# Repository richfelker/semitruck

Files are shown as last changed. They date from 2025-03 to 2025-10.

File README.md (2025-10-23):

# The Semitruck Extruder

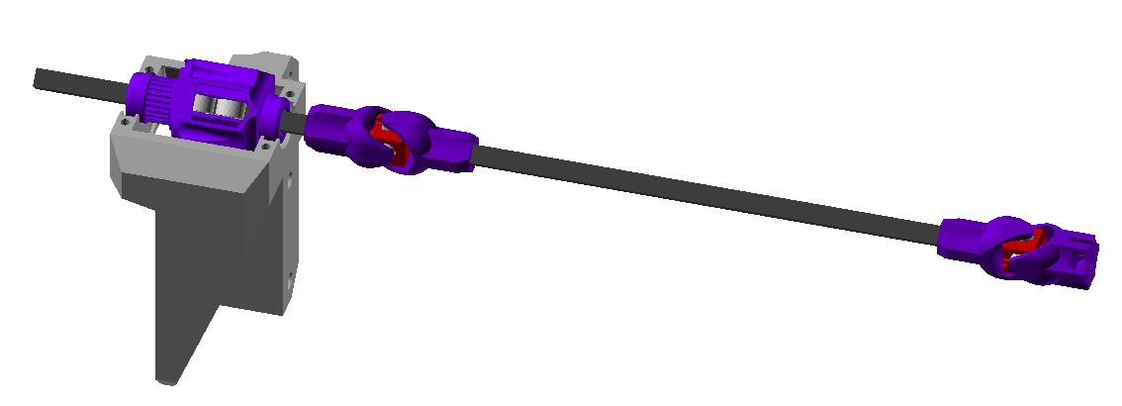
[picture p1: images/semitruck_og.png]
CAD diagram of Semitruck shaft


The Semitruck is a *rigid* remote direct drive (RDD) extruder based on
printed Cardan joints, square carbon fiber shaft, and a coupling that
transfers rotational force through ball bearings that can freely roll
along the four faces of the square shaft. It comes in two variants:

- OG Semitruck, where the vertical segment of the drive shaft engages
  with a fixed-position "slider gear" at the top of the printer and is
  free to move up and down, and

- Semitruck Prime, with a telescoping double Cardan shaft coupled
  directly to the motor at the top of the printer.

In either variant, the shaft drives an ultra-compact worm-based
extruder on the toolhead. This makes it possible to achieve,
simultaneously:

- Extremely low moving mass
- High extrusion speed
- High extrusion force
- Rapid high-precision pressure advance adjustments and retractions
- Near-zero backlash

The double Cardan shaft is net constant-velocity (CV), and is not
subject to position-dependent offset of the shaft angle. The latter
property sets it apart from most other RDD configurations, which rely
on large reduction gear ratios along with well chosen motor
positioning to minimize error.

The Semitruck has been operated at up to 90k mm/s² kinematic
accelerations and 60 mm³/s flow. It can achieve pressure advance
smooth times at least as low as 10 ms.

Like this project? Support it and my other work on Ko-fi or Patreon:

- https://ko-fi.com/daliasprints
- https://patreon.com/daliasprints

## Project Status

The OG Semitruck has been in public beta since May of 2025. It was
successfully operated on the original build of the M45 delta from 2023
to early 2025, and was successfuly reproduced during private beta.

The Semitruck Prime has been operated on the original build of the M45
delta since March of 2025. It entered public beta in October of 2025.

The Prime does not supersede the OG, but makes different tradeoffs
that might make it more or less suitable for different machine
configurations and scalings. Both variants will be treated as
first-class for the forseeable future.

## Prerequisites

For delta printers: room for mounting at the top center and clearance
equal to Z travel range above the printer. The exact height
constrtaints are explained below. If the printer has a closed top
cutting/drilling a small hole (between 10 and 22 mm) may be needed for
accommodate the shaft.

For fixed-gantry printers with bed moving down in Z: framing out a
mount above the gantry at height roughly 75% of build width/height
above the top of the toolhead.

Others: not recommended. While the Semitruck *can* be used with any
kinematic system, the needed shaft length and framing above the
printer will be disproportinate and probably unacceptable.

## Mounting Expectations

The toolhead side of the extruder has filament path and screw spacing
designed to mount to a Slice Mosquito or Mellow NF Crazy
heatsink/frame. Creating adapter plates for other mountings, or
variants to the extruder housing, should not be hard, but they are not
included with the official Semitruck distribution at this time.

The motor side of the extruder is designed to mount to the top of a
20-series T-slot or V-slot extrusion with M5 screws and T nuts. The
slider gear should be centered directly above the worm gear shaft on
the toolhead side when the toolhead is at the center of the bed.
Off-center installation may work but increases the stress on the
U-joints towards the edges of the bed and tightens the constraints on
the shaft part lengths.

## Bill of Materials

### OG Semitruck

#### Motor, pulley, and and mounting assembly

- LDO 42STH48-2804AC motor (1)
- M3 6 mm screws (4)
- 190-220 mm closed loop GT2 belt (1)
- M3 8 mm screw (1)
- M3 20 mm screws (4)
- M3 nut (5)
- M5 10 mm screw (3)
- M5 T nut (3)
- M5 washer (3)
- Printed `emotor_mount.stl` (1)
- Printed `bearing_clip.stl` (1)
- Printed `pulley_60T.stl` (1)

#### Slider gear assembly

- 603ZZ (3x9x5 mm) bearings (8)
- 6702ZZ (15x21x4) bearings (2)
- M2.5 4 mm button head screws (4)
- M2.5 nuts (4)
- Printed `slider_housing.stl` (1)
- Printed `slider_pulley.stl` (1)
- Printed `slider_insert.stl` (4)

#### Shaft assembly

- Square 6 mm x 6 mm x round 4 mm ID carbon fiber tube (1)
- MR63 (3x6x2 mm) bearings (8)
- M2.5 6 mm screw (1)
- M2.5 nut (1)
- Printed `ujoint_center.stl` (2)
- Printed `ujoint_arm.stl` (3)
- Printed `ujoint_3mmend.stl` or `ujoint_end.stl` (1)

### Semitruck Prime

#### Motor and mounting assembly

- Leadshine 42CM06 2.5A motor (1)
- M3 6 mm screws (4)
- (Machine-specific mounting platform)

#### Telescoping shaft assembly

- 603ZZ (3x9x5 mm) bearings (4)
- Square 6 mm x 6 mm outer by round 4 mm ID carbon fiber tube (1)
- Square 10 mm x 10 mm outer by square 8.5 mm x 8.5 mm inner carbon fiber tube (1)
- MR63 (3x6x2 mm) bearings (8)
- M2.5 6 mm screw (2)
- M2.5 nut (2)
- Printed `telescope_housing.stl` (1)
- Printed `telescope_insert.stl` (4)
- Printed `telescope_stabilizer.stl` (1)
- Printed `ujoint_center.stl` (2)
- Printed `ujoint_arm.stl` (1)
- Printed `ujoint_big.stl` (1)
- Printed `ujoint_motorend.stl` (1)
- Printed `ujoint_3mmend.stl` or `ujoint_end.stl` (1)

### Noncannonical (effector side) assembly based on HGX hob

(Skip this section if you are building the original version using the
discontinued NF Cannon gear set.)

- HGX extruder parts set (v1 or v2, see below) (1)
- 3mm steel shaft, at least 35 mm in length, to be cut
- 0.5 module 2 start worm gear, 7mm outer diameter by 12 mm length
- F3-8M (3x8x3.5 mm) thrust bearings (4)
- M2.5 6 mm screws (2)
- M2.5 25 mm screws (3)
- M2.5 nuts (3)
- M3 10 mm button head screws (2)
- M3 nuts (2)
- MR63 (3x6x2 mm) bearings (2)
- Printed `noncannonical_bottom.stl` (1)
- Printed `noncannonical_top.stl` (1)
- Printed `noncannonical_insert.stl` (1)
- Printed `noncannonical_insert_cover.stl` (1)
- Printed `wormwheel-hgxv1.stl` (1)

### Headcannon (effector side) assembly based on NF Cannon gears

(Skip this section if you will be using the HGX gears.)

- Mellow NF Cannon parts - set 2, without motor (1)
- F3-8M (3x8x3.5 mm) thrust bearings (2)
- F5-10M (5x10x4 mm) thrust bearings (2)
- M2.5 6 mm screws (2)
- M2.5 25 mm screws (3)
- M2.5 nuts (3)
- M3 10 mm button head screws (2)
- M3 nuts (2)
- MR63 (3x6x2 mm) bearings (2)
- Printed `headcannon_bottom.stl` (1)
- Printed `headcannon_top.stl` (1)
- Printed `headcannon_insert.stl` (1)
- Printed `headcannon_insert_cover.stl` (1)

### Recommended Sources

- HGX v1 gear set:
  https://www.aliexpress.com/item/3256808173742215.html

- HGX v2 gear set: Not yet supported.

- 0.5 module 2 start worm gear, 7mm outer diameter by 12 mm length:
  https://www.aliexpress.com/item/2255800266497667.html or
  https://www.aliexpress.com/item/3256804727007575.html

- Mellow NF Cannon parts: NOT RECOMMENDED. These are discontinued, and
  may be changed/incompatible if re-issued.

- Carbon Fiber:
  https://windcatcherrc.com/product/carbon-fiber-sq-outer-with-rnd-inner-tube-6mm-x-6mm-x-4mm-x-1000mm/

- Bearings:
  https://www.avidrc.com/product/8/metric-bearings/

## Printed parts

Pregenerated STL files are included with Semitruck release packages.
To build STLs from the OpenSCAD source files, the supplied `Makefile`
can be used in an environment with GNU `make` and the `openscad`
command line interface available. The individual `.scad` files can
also be processed manually in OpenSCAD, using the customizer UI to
select which subpart to generate then exporting the STL.

### Printed worm wheel

If building the Noncannonical (HGX) version with printed worm wheel,
the worm wheel should be printed with 0.14 mm layer height, 100%
infill, and random seams. A seam that is aligned across layers *may
lead to periodic artifacts* and should not be used. Printing this
requires a well-tuned printer and may require some iteration with
different settings depending on material shrinkage and other factors.
The provided source and STL are designed to real physical dimensions,
not any fudge factors for printing with a particular material.

The recommended material for the worm wheel is PET (not PETG). As the
worm wheel and thrust bearings against it need lubrication, it should
not be printed in materials incompatible with grease, such as ABS or
ASA. POM or nylon may be options if PET is not available, but they
have not been tested.

### Other printed parts

The toolhead-side insert parts should be printed with 0.1 mm layer
height and 100% infill for best results. Everything else can be
printed with 0.2 mm layer height, 1.0-1.2 mm shell thickness, and 20%
infill.

The toolhead side top and bottom housing need minor supports for the
nuts and bolt heads. No other parts need supports.

Primary development and testing was done with parts printed in PET.

The toolhead-side parts should ideally be printed in material with low
to no creep, and the filament path insert especially should avoid PLA
or other materials that soften at low temperatures, as it's possible
to pull heat up into it when retracting, especially if using long
retractions at end-of-print or when pausing to avoid oozing while
idle.

For the rest of the parts, any rigid material is probably okay, even
PLA.

## OG Semitruck build

### Shaft length calculations

In order for the extruder to reach the entire build volume, the
lengths of the middle and vertical shaft segments must be chosen
correctly.

First, work out the middle segment length. A good starting point is
not to go over 45° at the U-joints. To satisfy this on a delta, the
middle segment length should be at least √2 times the build radius. To
satisfy this on a square build area, the middle segment length should
be equal to one side of the square.

Next, determine the height the slider gear and motor should be mounted
at. The vertical distance between the bottom of the slider and the top
of the extruder housing on the toolhead (at max Z) must be at least 45
mm plus the length of the middle shaft segment.

Finally, the end shaft segment length may be worked out based on
toolhead at minimum Z and maximal distance from the origin, but it is
recommended **not** to compute it yet, instead waiting to cut the
shaft until after installation is checked.

### Cutting and assembling the shaft part

The middle shaft segment should be cut to exactly 32 mm shorter than
the length determined above. Each U-joint arm end adds 16 mm to the
length (measured between joint centers).

One U-joint arm end, both in the same orientation, should be pressed
onto each end of the middle shaft segment. They can be attached
permanently with epoxy if desired, but are designed such that press
fit should be sufficient.

Press a single U-joint arm end onto the end shaft segment (not yet cut
to length) and prepare the 5 mm shaft-clamp U-joint end that will
attach to the toolhead side of the extruder by installing the M2.5
hardware on it.

Place a pair of MR63 bearings onto the pegs of one arm end, then slide
them as a unit onto a U-joint center block until they snap into place.
Then, rotate the center block and repeat with the other side of the
joint. A screwdriver shaft can be inserted through the opening between
the arms to hold the center block if pressing the second side of the
joint on is popping the first side's bearings out of their snap-fit
slots.

Repeat for the second U-joint.

### Assembling the slider

The slider consists of a 4-part printed insert holding 8 bearings, an
outer housing, and a printed GT2-tooth-profile pulley integrated with
the cover for the housing.

Assemble half of the insert by pressing four 603ZZ bearings onto the
pegs of one insert piece, then pressing a second insert piece's pegs
into two of the bearings already on the first.

Repeat to assemble the second half of the insert, then press the two
halves together.

Press the insert into the housing.

Press four M2.5 nuts into the hexagonal insets on the cover
(integrated with the pulley), and attach it to the housing using the
four M2.5 4 mm button head screws.

Place the two 6702ZZ bearings over the two ends of the slider assembly
in preparation for slotting it into the motor mount assembly.

### Mounting the extruder motor

Attach the slider to the printed motor bracket with the closed loop
timing belt wrapped around it by pressing the two 6702ZZ bearings into
the slots. The belt should be captured. Press 4 M3 nuts into the slots
beside the bearings, and use the printed bearing clips, each with two
20 mm M3 screws, to secure the bearings.

(Note: The upper clip is optional, since belt tension will suffice to
secure the upper bearing. You may wish to omit it for ease of
disassembly.)

Loosely attach the motor with the 6 mm M3 screws, making sure it can
still slide freely for adjustment. Attach the printed 60T primary
pulley to the motor shaft using an M3 nut and 8 mm M3 screw to secure
the pinch coupler. Bring the timing belt around the pulley, pull the
motor until the belt is no longer slack, and verify vertical alignment
of the belt. If needed, loosen the clamp on the pulley and slide it
up/down on the motor shaft to align with the slider-side pulley, then
retighten. Pull the motor tight to tension the belt adequately, and,
while holding it, tighten down the four motor screws.

## Semitruck Prime build

### Shaft length calculations

The necessary parameters for determining shaft length and thereby
mounting height are the length $z$ of Z travel range immediately below
the motor and the maximum needed XY travel radius $r$ relative to the
center point just below the motor. A third parameter $k$ is a constant
determined by the geometry of the U-joint and telescopic joint parts,
and has a value of 61 mm for the standard parts.

In order to allow for error in mounting position, it is recommended
that the values $z$ and $r$ be padded by a few millimeters. However,
the location of the motor-end U-joint arm on the motor shaft allows
for some degree of adjustment, and motor shims may also be used if
needed.

In terms of these parameters, the shaft length $h$ measured between
U-joint centers is given by the formula:

$h = \frac{2k + z + \sqrt{4z^2 + 3r^2 + k^2 + 4kz}}{3}$

The length of the fully-extended shaft, measured between U-joint
centers, is then $2h-k$.

The inner carbon fiber square tube needs to be cut to a length of
$h-33$ mm.

The outer carbon fiber square tube needs to be cut to a length of
$h-52$ mm.

### Placement/mounting of motor

The motor needs to be mounted such that, with the toolhead at maximum
Z just below the motor, the shaft is at minimum length. This means the
motor-side U-joint center should be exactly $h$ mm above the
extruder-side U-joint center.

There is presently no standardized mounting setup for the Semitruck
Prime motor.

### Telescoping shaft assembly

The telescopic coupling consists of a 4-part printed insert holding 4
603ZZ bearings and a printed outer housing. Assemble the insert in a
cross shape by pressing two 603ZZ bearings onto the pegs of one insert
piece, then pressing a second insert piece's pegs into two of the
bearings already on the first. Repeat to assemble the second half of
the insert, then press the two halves together, and press the insert
into the housing.

Onto one end of the smaller carbon fiber tube, press fit the printed
stabilizer and verify that it fits into the larger carbon fiber tube
without any significant friction. If it does not, shave the outside of
the stablizer down until it does.

Push the end of the smaller tube without the stabilizer on it through
the telescopic coupling from the side with the square 10 mm socket.
The bearings should roll on it as you push it through. Press fit a
printed U-joint arm onto the exposed end of the tube so that it cannot
inadvertently slide back out.

Press fit the larger tube into the square 10 mm socket on the
telescopic coupling, letting the end of the smaller tube with the
stabilizer go inside the larger tube. Then, press fit the U-joint arm
with the 10 mm socket on the other end of the larger shaft, ensuring
that both U-joint arms are in the same orientation (coplanar).

Assemble the U-joint centers and motor/extruder side arms onto the
ends as in the OG Semitruck instructions.

## Toolhead side assembly

First, make sure you have the appropriate set of printed parts --
Noncannonical to use the HGX hob; Headcannon if you have and will be
using the discontinued Mellow NF Cannon gears.

### Filament path and idler assembly

First check that the filament path has clearance for filament. A 2 mm
diameter screwdriver shaft should fit through it with some friction,
and clear out any roughness or stringing that might be in the way.

Begin by assembling the filament path and idler bearing insert. Place
two MR63 bearings in the cutouts of the printed insert and slide the
printed insert cover over them. Place M3 nuts in the two hexagonal
cutouts in the cover, and insert and tighten 10 mm M3 button head
screws from the other side.

Before continuing, ensure that the filament path insert can fit into
the rectangular holes in the printed housing top and bottom parts.
Clean up any "elephant foot" or other print issues that might keep it
from fitting later.

### Hob and worm wheel

Now begin with the hob and worm wheel. If you are using the HGX hob,
you will need to separate it from the spur gear that came attached to
it. This can be done non-destructively for the HGX version 1. Insert a
thin flat tool such as a putty knife or razor blade between the
plastic gear and the filament hob, and lightly pry back and forth
until they can be pulled apart by hand. Alternatively, you may apply
pressure to the plastic pins through the hob to push the gear out.
Once the hob is separated, press the printed worm wheel onto it.

If using the NF Cannon gears, the gear on one of the two hobs already
serves as a worm wheel matching the worm. To check which one, hold the
gear and hob vertically with the axis running left/right, and look at
the slant of the teeth. The correct one is the one where the teeth
slant upward to the left and downward to the right.

Now, insert one of the needle bearings from the HGX or Cannon set in
the hob, and put the included shafts, 3 mm diameter and approximately
15.8 mm in length, through the center. Next, assemble the F3-8M thrust
bearings on the shaft. The races with the larger inner diameter, which
are loose and spin freely on the shaft, belong on the inside next to
the worm wheel and filament hob, with the grooves facing outward. The
balls go next, and the races with the smaller diameter go on the
outside, with the grooves facing inward towards the balls. They should
"snap" onto the shaft and not fall off easily. Before putting them on,
apply a small amount of grease.

### Worm gear

If using the HGX, the worm gear must be pressed onto the 3 mm shaft.
This can be done without any specialized tooling beyond a hammer, 4 mm
washer, and small socket. Place the worm on top of the socket with one
or more washers in between, and hammer the end of the shaft until
3-3.5 mm of it extend out the other end of the worm.

If you are using the NF Cannon gears, insert the 5 mm diameter shaft
through the worm with 4-4.5 mm extending out the threaded side and
tighten the set screw on the worm sleeve.

Now, assemble the thrust bearings on the shaft. The process is the
same for either version. This time, the smaller ID races go on first,
next to the worm. The fit should be very tight, and may also require a
press or hammering using the same technique as above. The balls and
outer races will be loose until installation; for now, just grease
them.

### Housing

Begin by pressing 3 M2.5 nuts into the holes in the bottom part of the
housing. Turn it upright, and place the hob/worm wheel assembly with
the bearings in the halfround cutouts, with the hob on the side facing
the rectangular hole and the worm wheel on the side facing the round
hole.

Before continuing, insert the 6 mm M2.5 button head screws in the
two holes beside the rectangular filament path hole. Depending on
which variant you are building, they may be difficult to insert or
remove later.

Next, place the filament path insert in the rectangular hole.

Finally, place the outer race of the worm thrust bearing in the circular
hole, being sure the groove is facing upward. Apply some grease and
place the ball cage and worm assembly on top, with the long side of
the shaft pointing upward. Grease the other ball cage and place it on
top, followed by the final thrust bearing outer race, with the groove
facing downward.

Line up the top of the housing and press it closed on top of the
bearings and filament path. Insert three 25 mm M2.5 screws to secure
it to the bottom part.

With the screws tightened, there should be no vertical play in the
worm. If this is not the case, due to manufacturing variance in the
worm, printing inaccuracy, or other factors, it will be necessary to
shim the top side, either between the worm and thrust bearing, or
between the thrust bearing and housing, with a suitably sized washer
or printed part. It is critical that the worm be well-constrained
vertically; otherwise the extruder will have catastrophic backlash and
print quality will be very poor.

It should be difficult to turn the worm by hand, but possible by
gripping the shaft with tools or a drill chuck, or with the printed
U-joint arm end. At this point you can test feeding filament through
manually by turning the worm.

## Installing the square shaft

Move the toolhead out of the way well below maximum Z, and insert the
end shaft segment up through the bottom of the slider. The fit should
be somewhat tight, turning the bearings inside the slider as it's
moved. Raise the shaft until the joint at the lower end is higher than
the top of the toolhead, then bring it down onto the worm gear shaft
and clamp it in place by tightening the screw.

## Firmware Configuration

### Noncannonical (HGX based) configuration

The HGX hob has a measured pitch circumference of 56.94 mm, and the
worm gear reduction ratio is 36:2 (18:1). The motor-side pulley
gives a 24:60 (2:5) increase in speed. If using Klipper, these values
can be entered directly without having to do any math:

    [extruder]
    rotation_distance: 56.94
    gear_ratio: 24:60, 36:2

To convert to E-steps-per-mm for other firmware, some math is needed.
Applying the gear ratios, this is 7.90833 mm of filament advance per
rotation of the E motor, or 25.2898 **full steps** per mm. At 16
microsteps per step, that comes to 404.636 E-steps-per-mm.

### Headcannon (NF Cannon gearset based) configuration

The Cannon hob has a pitch circumference documented by Mellow as 59.08
mm, and the worm gear reduction ratio is 39:2 (19.5:1). The motor-side
pulley gives a 24:60 (2:5) increase in speed. If using Klipper, these
values can be entered directly without having to do any math:

    [extruder]
    rotation_distance: 59.08
    gear_ratio: 24:60, 39:2

To convert to E-steps-per-mm for other firmware, some math is needed.
Applying the gear ratios, this is 7.57435 mm of filament advance per
rotation of the E motor, or 26.4049 **full steps** per mm. At 16
microsteps per step, that comes to 422.478 E-steps-per-mm.

### In general

Polarity of the E motor step direction pin will vary depending on
motor wiring. It may be determined experimentally, or set directly to
whichever polarity is known to make the motor spin clockwise (viewed
from the output side).

Additional recommended starting points for settings with Klipper:

    [extruder]
    max_extrude_only_velocity: 45
    max_extrude_only_accel: 4000
    microsteps: 64
    pressure_advance: 0.036
    pressure_advance_smooth_time: 0.010
    
    [firmware_retraction]
    retract_length: 0.20
    # Speeds set way above limit so M220 won't slow down retracts
    retract_speed: 200
    unretract_speed: 200
    
    [tmc5160 extruder]
    run_current: 2.8
    stealthchop_threshold: 0
    interpolate: false

The above TMC configuration should be adapted to your particular
drivers. If they do not support the full current for the motor, it may
be necessary to run at lower retraction acceleration and/or increase
the pressure advance smooth time window.

## Mechanical Validation & First Runs

Once the Semitruck is mounted and configured, start off with manual
motion tests through your printer's UI to check that the shaft slides
freely up and down the slider and does not bind. Motion at low Z
height (upper shaft extended down as far as possible) is the hardest
case, and should be checked at the edges of the build area starting
with short moves, so that binding can be caught before it breaks
anything.

The usual fault mode, if it does break, is explosion of the U-joints,
which are low enough in mass that they should not pose severe danger,
but the bearings can easily be lost if this happens.

If binding is occurring, it may be necessary to mount the motor higher
and use a longer middle shaft segment, but first check that the slider
gear is not too tight on the shaft. This can occur as a result of
printing defects, and can usually be remedied by scraping/sanding the
inside of the slider housing (or reprinting it with very minor
horizontal offset to compensate) so that the bearings are not squeezed
as tightly against the shaft. It's also possible to run the system
restricted to a smaller build radius until the problem is resolved.

Before actual printing, extrusion rate should also be checked to
ensure that the motor is turning in the right direction and that the
correct amount of filament is being advanced. This can be done though
standard methods -- marking a known length of filament going into the
extruder, commanding extrusion of the same length, and verifying that
the marked spot ends at the point of entry to the extruder.

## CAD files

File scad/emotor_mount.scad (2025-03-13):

module emotor_mount() difference() {

	intersection() {
		linear_extrude(height=52,center=true,convexity=3)
		difference() {
			translate([-80,-8-42/2])
			square([80+16,8+42+20]);

			translate([16,0])
			circle(d=17.5);

			hull() for (x=[-80+16.5,-4-16.5])
			translate([x,0])
			circle(d=31-9);

			difference() {
				union() for (i=[0,1]) mirror([0,i])
				hull() for (x=[-80+5.5,-4-5.5])
				translate([x,31/2])
				circle(d=3.3);
				for (i=[1:3]) translate([-80+i/4*(-4+80),0])
				square([0.2,100],center=true);
			}
		}

		union() {
		rotate([90,0,0])
		linear_extrude(height=100,center=true,convexity=3)
		polygon([
			[16,26],[-1,26],[-5,20-11],
			[-80,20-11],[-80,20-11-4],
			[-4,-26],[16,-26]
		]);
		translate([-90,42/2,-52/2])
		cube([90+16,20,52-6-11]);
		}

		rotate([90,0,90])
		linear_extrude(height=200,center=true,convexity=3)
		polygon([
			[-21,20+6],[-21-8,20],
			[-21-8,-20],[-21,-20-6],
			[21+20,-20-6],[21+20,0],
			[21+8,0],[21+8,20],[21,20+6]
		]);
	}

	// bearings cutouts
	translate([16,0,0]) {
		cylinder(d=34.5,h=40,center=true);
		*translate([0,0,-20])
		linear_extrude(height=40,convexity=3)
		rotate(30) hexagon(34);
		translate([0,0,-20+29/2])
		hull() {
			cube([40,20,29],center=true);
			translate([-4,0,0])
			cube([40,20,21],center=true);
		}
		for (i=[0,1]) mirror([0,0,i])
		translate([0,0,20+1])
		cylinder(d=21.1,h=4.1);
		for (i=[0,1],j=[0,1]) mirror([0,0,i]) mirror([0,j,0])
		translate([0,14,20+2+1])
		rotate([0,-90,0]) {
			cylinder(d=3.1,h=100,center=true);
			translate([0,0,15])
			rotate(30)
			linear_extrude(height=100,convexity=3)
			hexagon(5.5);
		}
	}

	// belt cutout
	*translate([-100/2,-46/2,20-10])
	cube([100,46,10]);
	hull() {
		translate([16,0,20-10])
		cylinder(d=32,h=9);
		translate([-42/2-4,0,20-10])
		cylinder(d=60,h=9);
	}

	// motor cutout
	translate([-90,-46/2,-42+20-11-4])
	cube([90-2,46,42]);

	// motor screw cutouts
	for (i=[0,1]) mirror([0,i,0])
	hull() for (x=[-80+5.5,-4-5.5])
	translate([x,31/2,20-11-2])
	cylinder(d=5.8,h=10);

	// chamfers
	let (cs=16/sqrt(2))
	for (p=[
		[16,-42/2-8,-60],
		[16,42/2+8,0],
		[16,42/2+20,-60],
		[-80,-42/2-8,-60],
		[-80,42/2+20,-60],
	])
	translate(p)
	rotate(45)
	translate([0,0,100/2])
	cube([cs,cs,100],center=true);

	// curve over extrusion
	translate([0,42/2+20,0])
	rotate([0,90,0])
	cylinder(r=12,h=200,center=true);

	// extrusion cutout
	translate([0,21+20/2+1,-20/2-52/2+8])
	cube([200,20+2,20],center=true);

	// extrusion mount holes
	for (p=[
		[16-8,42/2+10,0],
		[-80+8,42/2+10,0],
		[(-80+16)/2,42/2+10,0],
	])
	translate(p)
	translate([0,0,-52/2+8])
	{
		cylinder(d=5.5,h=100,center=true);
		translate([0,0,4.4])
		cylinder(d=10.5,h=100);
		*translate([0,0,8.4])
		cylinder(d=12,h=100);
	}

// extrusion
*%translate([0,21+20/2,-20/2-52/2+8])
cube([200,20,20],center=true);

// motor
*%translate([-30,0,-48/2+40/2-11-4])
cube([42,42,48],center=true);
}


if (0) {
difference() {
	translate([20/2-4,0,0])
	cube([20,42,52],center=true);
	translate([16,0,0]) {
		cylinder(d=32,h=40,center=true);
		cylinder(d=17,h=100,center=true);
		for (i=[0,1]) mirror([0,0,i])
		translate([0,0,20+1])
		cylinder(d=21,h=4);
	}
}

translate([-70/2,-11/2+42/2,40/2-9-5/2])
cube([70,11,5],center=true);
}




rotate([0,90,0])
emotor_mount();

use <slider.scad>;
*color("#202080")
translate([0,0,-16])
rotate([0,-90,0])
translate([0,0,-7])
slider_assembly();

module hexagon(w) polygon([for (i=[1:6]) w/sqrt(3) * [cos(60*i), sin(60*i)]]);

$fs=.2;
$fa=5;

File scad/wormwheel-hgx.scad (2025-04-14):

use <wormwheel.scad>;

// HGX hob version to couple with
version = 1;

// Worm gear pitch radius
wr = 2.92;

// Worm gear starts
starts = 2;

// Worm gear modulus
modulus = 0.5; // 0.1

// Worm wheel tooth count
nteeth = 36;

worm_profile = [
	[0,1.52/2],
	[1/8,1.52/2],
	[2/8,-1.52/4],
	[6/8,-1.53/4],
	[7/8,1.53/2],
	[1,1.53/2]
];

module hgx_worm_wheel(profile,radius,starts,modulus,teeth,hob_extra=0.1,tb_extra=0.14,thickness=5) {
	difference() {
		worm_wheel(profile=profile,radius=radius,starts=starts,modulus=modulus,teeth=teeth,thickness=thickness);
		translate([0,0,thickness/2-3]) {
			d=7.55+0.15;
			cylinder(d=d,h=10);
			translate([0,0,thickness/2-hob_extra])
			cylinder(d1=d,d2=d+0.75,h=0.55);
			cylinder(d=3.7,h=100,center=true);
		}
		translate([0,0,5/2-hob_extra])
		cylinder(d=modulus*teeth*2,h=2*hob_extra);
		translate([0,0,-5/2+tb_extra]) mirror([0,0,1])
		cylinder(d=modulus*teeth*2,h=2*tb_extra);
	}
	for (a=[0,180]) rotate(a)
	translate([9/2+2.9/2,0,thickness/2-hob_extra]) {
		cylinder(d1=2.95,d2=2.88,h=2);
		translate([0,0,2])
		cylinder(d1=2.88,d2=1.88,h=0.5);
	}
}

hgx_worm_wheel(profile=worm_profile,radius=wr,starts=starts,modulus=modulus,teeth=nteeth);

$fs = $preview ? 0.5 : .2;
$fa = $preview ? 15 : 5;

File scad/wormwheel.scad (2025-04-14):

function helix_section(profile,r,starts,n=0) = [
	for (fn=[n>0 ? n : $fn>0 ? $fn :ceil(360/$fa)])
	for (i=[0:fn]) [cos(360*i/fn),sin(360*i/fn)]*(r+lookup((i*starts/fn)%1.0,profile))
];

worm_profile = [
	[0,1.52/2],
	[1/8,1.52/2],
	[2/8,-1.52/4],
	[6/8,-1.53/4],
	[7/8,1.53/2],
	[1,1.53/2]
];

module worm(profile=worm_profile,radius,starts,modulus,length) {
	lead=PI*starts*modulus;
	linear_extrude(height=length,twist=-360*length/lead,convexity=3)
	polygon(helix_section(profile,radius,starts));
}

module worm_wheel(profile=worm_profile,radius,starts,modulus,teeth,thickness)
difference() {
	cylinder(d=modulus*teeth+1.5,h=thickness,center=true);
	for (i=[1:$preview?2:0.5:teeth]) rotate(360*i/teeth)
	translate([modulus*teeth/2+radius,0,0])
	rotate([90,0,0])
	translate([0,0,-2*PI])
	rotate(360/starts * (i%1.0))
	worm(profile=profile,radius=radius,starts=starts,modulus=modulus,length=4*PI);
}

$fs = 0.2;
$fa = 5;

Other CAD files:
scad/bearing_clip.scad
scad/gt2.scad
scad/headcannon.scad
scad/noncannonical.scad
scad/pulley.scad
scad/slider.scad
scad/telescope.scad
scad/ujoint.scad

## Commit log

2025-03-13 initial check-in
    [bearing_clip.scad, emotor_mount.scad, gt2.scad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]
2025-03-13 ujoint: slim down to increase usable joint angle, avoid interference
    [ujoint.scad]
2025-03-13 ujoint: remove old code no longer in use
    [ujoint.scad]
2025-03-13 ujoint: chamfer square shaft entry point
    [ujoint.scad]
2025-03-15 ujoint: fix breakage in end arm where clamping hardware no longer fit
    this was an oversight in the previous slimming change. add back half
    the difference and move the screw down slightly so it still fits.
    [ujoint.scad]
2025-03-16 ujoint: add big variant for 10 mm square shaft
    this will be needed for the semitruck prime.
    [ujoint.scad]
2025-03-31 headcannon: redesign idler holder cover
    the old idler holder clamped the idler bearings against the tiny
    spacers, driving the spacers into the open channel and destroying the
    bearings if the screws were sufficiently tightened, and failing to
    hold the idlers well if not.
    the new design has the cover walls clamping against the main insert
    body walls so that the clamping force is not on the bearing spacers.
    [headcannon.scad, ujoint.scad]
2025-03-31 headcannon: non-invasive changes to clean up parametrization
    [headcannon.scad]
2025-03-31 headcannon: use worm wheel OD explicitly, remove unused old code
    this sets the stage for changing to use of pitch radius elsewhere.
    [headcannon.scad]
2025-03-31 headcannon: use pitch diameter/radius for worm and worm wheel
    previously wwr was outer radius of worm wheel and wr was a
    pseudo-radius chosen such that wwr+wr was the correct center distance
    between the worm and worm wheel. now both wwr and wr are pitch radius.
    [headcannon.scad]
2025-04-01 headcannon: incorporate bite into hob pitch radius, make it one-sided
    introduce a second parameter for idler bearing preload offset, copying
    the default from bite which was previously used. it should actually be
    set much lower.
    [headcannon.scad]
2025-04-01 headcannon: adjust filament path, bite, preload
    these values were previously gussed, partly based empirical feedback
    using the poor idler insert geometry that was not sufficiently rigid.
    the new values are based on actual data.
    idler preload is set to allow 0.02 mm of play in the MR63 bearing and
    0.05 mm of M3 thread radius below 3 mm (expected diameter is 2.927
    mm).
    bite was measured using actual filament compressed between a pair of
    hobs and taking half the value for a single hob.
    offset is now computed to have the filament go straight up/down off
    the idler bearings.
    [headcannon.scad]
2025-04-01 headcannon: fix missing parameterization of worm position
    [headcannon.scad]
2025-04-12 headcannon: add "noncannonical" version for hgx gears
    initially this is still configured to use the nf cannon worm. this
    will be changed to an actually-sourceable, lighter worm in a separate
    step.
    [noncannonical.scad]
2025-04-12 headcannon: expose mounting mockup and angle parameter
    [headcannon.scad]
2025-04-12 headcannon: factor worm bolt angles as a parameter
    [headcannon.scad]
2025-04-12 headcannon: factor worm wheel bolt positions as a parameter
    [headcannon.scad]
2025-04-12 headcannon: rearrange bolts to eliminate one of the four
    the primary goal here is to solve an interference with delta arms from
    the bolt point nearest the A tower, but after rotating the worm bolts
    the other direction, there's no reason to have one right next to the
    worm wheel bolt. instead let one bolt serve both roles, which reduces
    mass a bit as a bonus.
    [headcannon.scad]
2025-04-12 headcannon: make worm thrust bearing diameter a parameter
    [headcannon.scad]
2025-04-12 headcannon: make worm bearing holder honor parameter
    [headcannon.scad]
2025-04-12 headcannon: parameterize worm outer diameter/clearance
    [headcannon.scad]
2025-04-12 headcannon: ensure bearing fits when worm is smaller than bearing
    [headcannon.scad]
2025-04-14 headcannon: make worm bearing thickness and spacing parametrized
    the entire assembly height is still wrongly derived from the base worm
    length (now described as mating length), so any additional length
    needs to be nominally in the "sleeve" so as not to break other things.
    this should suffice for building with an alternate worm gear.
    [headcannon.scad]
2025-04-14 noncannonical: update for new worm & new parameters
    [noncannonical.scad]
2025-04-14 headcannon: fix typo in geometry that broke printability
    [headcannon.scad]
2025-04-14 noncannonical: fix bearing thickness, mounting interference
    thrust bearing for 3mm ID is 3.5 mm thick, not 4 mm.
    one worm wheel bolt post needs to be moved slightly not to interfere
    with mounting screws.
    [noncannonical.scad]
2025-04-14 ujoint: fix erroneously applied change from unrelated commit
    [ujoint.scad]
2025-04-14 ujoint: improve pinch, add variants for motor D shaft and 3 mm worm shaft
    the motor shaft variant does not bottom out but lets the shaft go
    through, so it can be placed as close as possible to the motor body.
    the variant for 3mm shaft has an extra 2 mm of pinch engagement, and
    zero clearance, in order to compemnsate for loss of mechanical
    advantage in the pinch interface.
    the pinch cut for all variants it updated to be longer, so that the
    last bit of engagement isn't wasted and unable to pinch tight.
    [ujoint.scad]
2025-04-14 wormwheel: add to repository and build recipes
    [wormwheel-hgx.scad, wormwheel.scad]
2025-04-14 build: don't rebuild stls every time stl dir is modified
2025-04-15 docs: update with hgx hob option & changes to toolhead assembly
2025-04-15 ujoint: cleanup, rename modules appropriately for use from other files
    [ujoint.scad]
2025-04-15 ujoint: reorient for printability with rear seam
    [ujoint.scad]
2025-04-15 slider: disable extra mockups in assembly preview for now
    [slider.scad]
2025-04-18 headcannon/noncannonical: improve filament path printability
    the old worm wheel side clearance did not take into account that the
    hob has an extra 0.9 or more of metal before the worm wheel starts.
    this had the cutout cutting unnecessarily low into the filament path
    insert, making the bearing holes at least in the noncannonical version
    cut through the top to the worm wheel cutout zone. reduce the excess
    clearance so that does not happen.
    also, the overhang over the bearing holes was sloped a lot more than
    it needed to be in order to be printable. this also contributed to the
    frailty of the top, so flatten it out a bit. there was already a
    factor for this from long ago, but it was never tune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
    [headcannon.scad]
2025-04-18 docs: add toolhead assembly instructions, amend BOM
2025-04-23 docs: fill in missing BOM sources
2025-04-23 docs: add simple assembly image
    eventually this should be generated reproducibly in the repo, but I'm
    having trouble getting that to work, so a hard-coded image will have
    to do for now.
2025-10-11 telescope: add new parts for telescoping semitruck prime shaft
    [telescope.scad]
2025-10-23 telescope: remove cruft left from forking off OGST slider gear
    [telescope.scad]
2025-10-23 docs: add st prime bom and basic instructions
    documenting this is a work in progress and may not be entirely
    complete or accurate yet.
2026-04-25 ujoint: fix missing else that caused rotation not to apply to else chain
    [ujoint.scad]
2026-04-25 ujoint: remove some useless material on ends
    this is mainly aesthetic but is also interferes less with filament
    feed tube or screw heads nearby.
    [ujoint.scad]
2026-04-25 ujoint: move pinch screw up 1 mm to cut off some more material
    [ujoint.scad]
2026-05-10 ujoint: strengthen pinch surfaces held by screw
    [ujoint.scad]
2026-05-10 ujoint: move pinch screw closer to shaft on 3mm shaft
    it should be a fixed distance from the shaft radius not from the shaft
    center.
    [ujoint.scad]
2026-05-10 mostly revert previous pinch regression moving screw up
    undo most of commit c0593eb7e5000db18d90791b1fd66f8440142ea6.
    [ujoint.scad]
2026-05-10 telescope: update stabilizer to work, not need postprocessing
    any wide zones of friction will bind, so limit the stabilization to 4
    tiny points at the end of the shaft. empirically, 0.28 mm on each side
    (8.56 mm width against a nominally 8.5 mm ID large shaft) seems good.
    slightly larger may work too; much smaller and it will have rattling.
    in some sense this is a stopgap for what could be done better by
    switching to a 12 mm OD round outer shaft that would fit a better
    mechanism, but it's a reasonable QoL improvement for now.
    [telescope.scad]
2026-05-14 ujoint: add end variant for 7mm OD shaft collar with grubs
    the 3mm shaft is hard to reliably grip with a plastic pinch interface,
    and if it slips, the friction ruins the pinch interface. the new
    version her fits a 3mm ID, 7mm OD, 8mm length collar with grub screws
    spaced at a 90° angle, and allows access to the grubs.
    [ujoint.scad]
2026-05-17 ujoint: fix preview of joint connection
    it was using an outdated model name and not rotated to match part.
    [ujoint.scad]
